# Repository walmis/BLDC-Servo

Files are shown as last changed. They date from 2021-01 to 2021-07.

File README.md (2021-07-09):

# BLDC-Servo

This project implements a FOC motor controller board for 57BLF0x series NEMA brushless motor.

The project goals are:
* to be inexpensive
* fully support FOC drive
* smooth operation for FFB devices
* Large stalled torque == relatively large current drive

The main components are:
* STM32L412 or STM32F103C8T6 MCU
* NCP81151 - MOSFET Gate drivers
* NCS213/INA213 current sense amplifiers
* FDMS8018 N-channel MOSFETS (can be any TDSON-8 30V>= MOSFETS with required current rating)
* MP2359 DC-DC step-down
* SN75176B RS485 transceiver

The board attaches directly to the motor casing with mosfets in direct contact (with thermal paste). This makes a good heatsink for power dissipation.

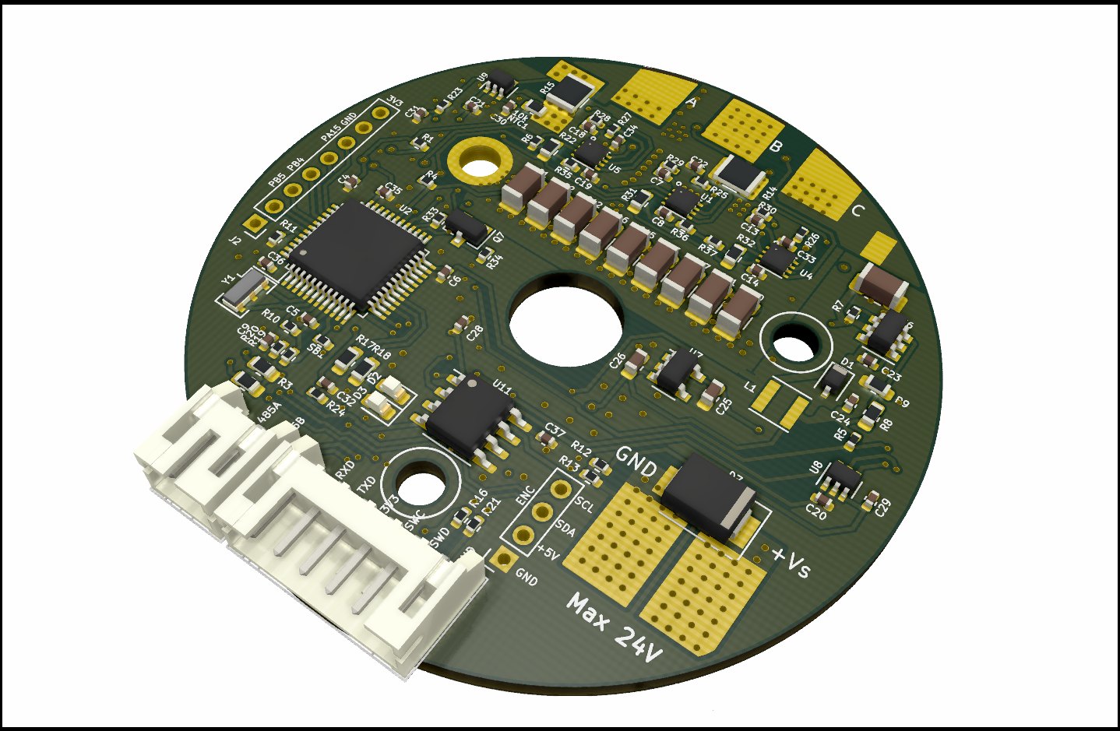
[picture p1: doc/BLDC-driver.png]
Board top

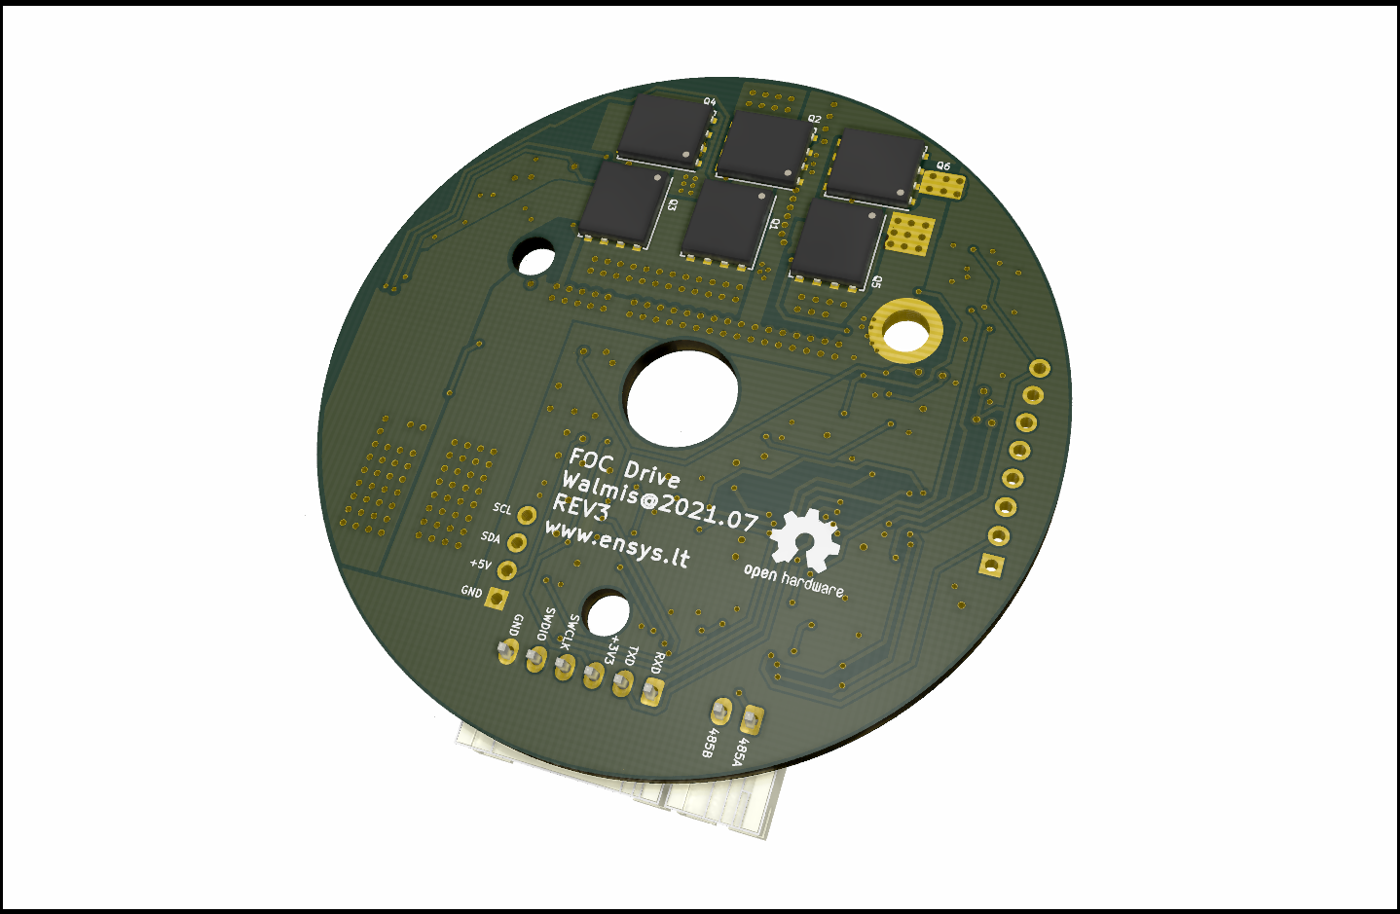
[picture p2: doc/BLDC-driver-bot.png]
Board bottom


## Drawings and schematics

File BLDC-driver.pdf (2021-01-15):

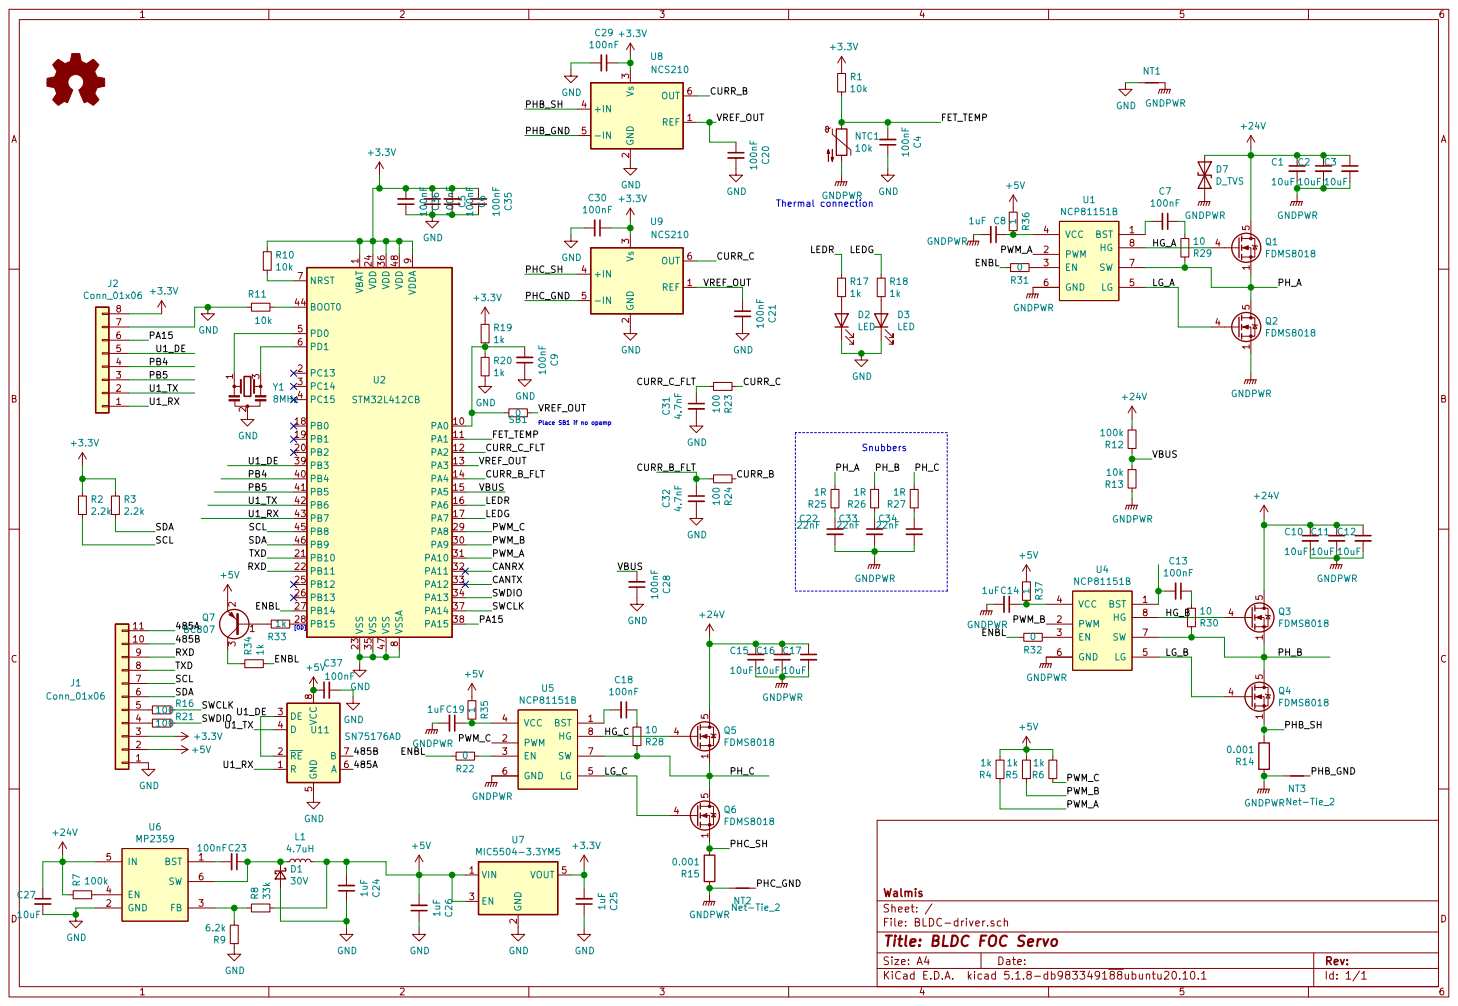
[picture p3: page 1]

1 VDD 24 VDD 36 VDD 48 VDDA

9 VSS 23 VSS 35 VSS 47 VSSA

File: BLDC-driver.sch Sheet: / Walmis

Id: 1/1 Title: BLDC FOC Servo

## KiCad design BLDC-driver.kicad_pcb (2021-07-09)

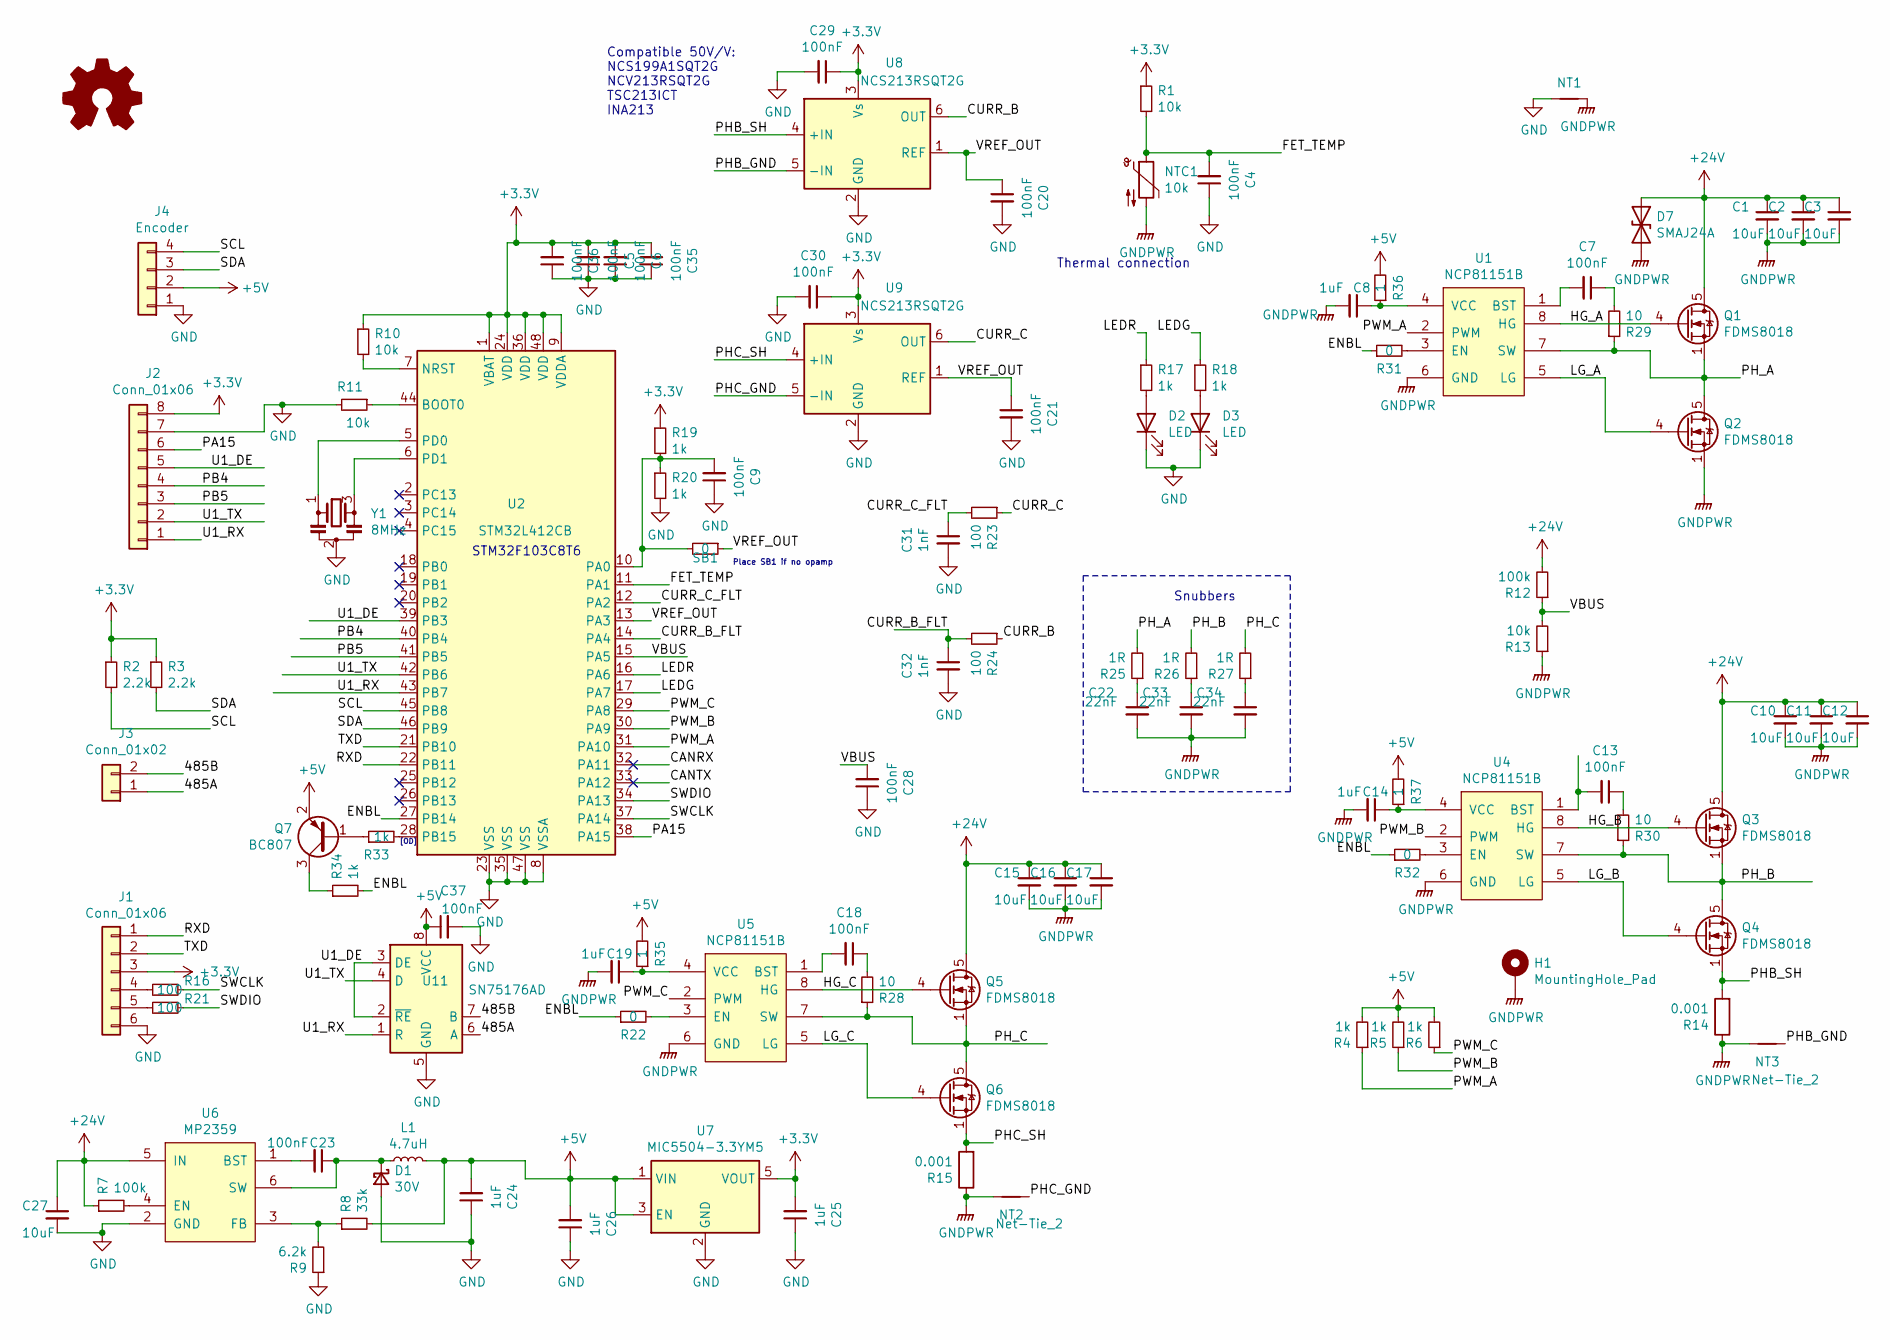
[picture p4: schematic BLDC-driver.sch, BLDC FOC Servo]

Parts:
C1, C2, C3, C10, C11, C12, C15, C16, C17, C27: 10uF; C_1206_3216Metric; JLCSMT C13585
C4, C5, C6, C7, C9, C13, C18, C20, C21, C23, C28, C29, C30, C35, C36, C37: 100nF; C_0402_1005Metric; JLCSMT C1525
C8, C14, C19, C24: 1uF; C_0402_1005Metric; JLCSMT C52923
C22, C33, C34: 22nF; C_0402_1005Metric; JLCSMT C1532
C25, C26: 1uF; C_0603_1608Metric; JLCSMT C15849
C31, C32: 1nF; C_0402_1005Metric; JLCSMT C1523
D1: 30V; D_SOD-323
D2: LED; LED_0603_1608Metric; JLCSMT C2286
D3: LED; LED_0603_1608Metric; JLCSMT C72043
D7: SMAJ24A; D_SMB; MPN SMAJ24A-E3/61
H1: MountingHole_Pad; MountingHole_3.2mm_M3_DIN965_Pad
J1: Conn_01x06; JST_PH_S6B-PH-K_1x06_P2.00mm_Horizontal
J2: Conn_01x06; PinHeader_1x08_P2.00mm_Vertical
J3: Conn_01x02; JST_PH_S2B-PH-K_1x02_P2.00mm_Horizontal
J4: Encoder; PinSocket_1x04_P2.00mm_Vertical
L1: 4.7uH; L_Taiyo-Yuden_MD-3030
NT1, NT2, NT3: Net-Tie_2; NetTie-2_SMD_Pad0.5mm
NTC1: 10k; R_0603_1608Metric; MPN NCU18XH103F60RB
Q1, Q2, Q3, Q4, Q5, Q6: FDMS8018; TDSON-8-1
Q7: BC807; SOT-23; JLCSMT C8326
R1, R10, R11, R13: 10k; R_0402_1005Metric; JLCSMT C25744
R2, R3: 2.2k; R_0603_1608Metric; JLCSMT_PKG 0603
R4, R5, R6, R19, R20, R33, R34: 1k; R_0402_1005Metric; JLCSMT_PKG 0402
R7, R12: 100k; R_0402_1005Metric; JLCSMT C25741
R8: 33k; R_0603_1608Metric; JLCSMT C4216
R9: 6.2k; R_0603_1608Metric; JLCSMT_PKG 0603
R14, R15: 0.001; R_1210_3225Metric; MPN PMR25HZPFV1L00; JLCSMT C154629
R16, R21, R23, R24: 100; R_0402_1005Metric; JLCSMT_PKG 0402
R17, R18: 1k; R_0603_1608Metric; JLCSMT_PKG 0603
R22, R31, R32: 0; R_0603_1608Metric; JLCSMT C21189
R25, R26, R27: 1R; R_0402_1005Metric; JLCSMT_PKG 0402
R28, R29, R30: 10; R_0402_1005Metric; JLCSMT_PKG 0402
R35, R36, R37: 1; R_0402_1005Metric; JLCSMT C25086
SB1: 0; R_0402_1005Metric; JLCSMT C17168
U1, U4, U5: NCP81151B; DFN-8-1EP_2x2mm_P0.5mm_EP0.9x1.5mm; MPN NCP81151MNTBG
U2: STM32L412CB; LQFP-48_7x7mm_P0.5mm
U6: MP2359; SOT-23-6; JLCSMT C14259
U7: MIC5504-3.3YM5; SOT-23-5
U8, U9: NCS213RSQT2G; SOT-363_SC-70-6
U11: SN75176AD; SOIC-8_3.9x4.9mm_P1.27mm; JLCSMT C7063
Y1: 8MHz; Resonator_SMD_muRata_CSTxExxV-3Pin_3.0x1.1mm

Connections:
+3V3: C5.2, C6.2, C25.2, C29.1, C30.1, C35.2, C36.2, J1.3, J2.8, R1.1, R2.1, R3.1, R10.1, R19.1, U2.1 (VBAT), U2.9 (VDDA), U2.24 (VDD), U2.36 (VDD), U2.48 (VDD), U7.5 (VOUT), U8.3 (Vs), U9.3 (Vs)
+5V: C24.2, C26.2, C37.1, J4.2, L1.2, Q7.2 (E), R4.2, R5.2, R6.2, R8.2, R35.2, R36.2, R37.2, U7.1 (VIN), U7.3 (EN), U11.8 (VCC)
+24V: C1.1, C2.1, C3.1, C10.1, C11.1, C12.1, C15.1, C16.1, C17.1, C27.1, D7.1 (A1), Q1.5 (D), Q3.5 (D), Q5.5 (D), R7.1, R12.2, U6.5 (IN)
/485A: J3.1, U11.6 (A)
/485B: J3.2, U11.7 (B)
/CANRX: U2.32 (PA11)
/CANTX: U2.33 (PA12)
/CURR_B: R24.1, U8.6 (OUT)
/CURR_B_FLT: C32.1, R24.2, U2.14 (PA4)
/CURR_C: R23.1, U9.6 (OUT)
/CURR_C_FLT: C31.1, R23.2, U2.12 (PA2)
/ENBL: R22.1, R31.1, R32.1, R34.2, U2.27 (PB14)
/FET_TEMP: C4.2, NTC1.1, R1.2, U2.11 (PA1)
/HG_A: Q1.4 (G), U1.8 (HG)
/HG_B: Q3.4 (G), U4.8 (HG)
/HG_C: Q5.4 (G), U5.8 (HG)
/LEDG: R18.1, U2.17 (PA7)
/LEDR: R17.1, U2.16 (PA6)
/LG_A: Q2.4 (G), U1.5 (LG)
/LG_B: Q4.4 (G), U4.5 (LG)
/LG_C: Q6.4 (G), U5.5 (LG)
/PA15: J2.6, U2.38 (PA15)
/PB4: J2.4, U2.40 (PB4)
/PB5: J2.3, U2.41 (PB5)
/PHB_GND: NT3.2, U8.5 (-IN)
/PHB_SH: Q4.1 (S), Q4.2 (S), Q4.3 (S), R14.2, U8.4 (+IN)
/PHC_GND: NT2.2, U9.5 (-IN)
/PHC_SH: Q6.1 (S), Q6.2 (S), Q6.3 (S), R15.2, U9.4 (+IN)
/PH_A: Q1.1 (S), Q1.2 (S), Q1.3 (S), Q2.5 (D), R25.2, R29.1, U1.7 (SW)
/PH_B: Q3.1 (S), Q3.2 (S), Q3.3 (S), Q4.5 (D), R26.2, R30.1, U4.7 (SW)
/PH_C: Q5.1 (S), Q5.2 (S), Q5.3 (S), Q6.5 (D), R27.2, R28.1, U5.7 (SW)
/PWM_A: R4.1, U1.2 (PWM), U2.31 (PA10)
/PWM_B: R5.1, U2.30 (PA9), U4.2 (PWM)
/PWM_C: R6.1, U2.29 (PA8), U5.2 (PWM)
/RXD: J1.1, U2.22 (PB11)
/SCL: J4.4, R2.2, U2.45 (PB8)
/SDA: J4.3, R3.2, U2.46 (PB9)
/SWCLK: R16.1, U2.37 (PA14)
/SWDIO: R21.1, U2.34 (PA13)
/TXD: J1.2, U2.21 (PB10)
/U1_DE: J2.5, U2.39 (PB3), U11.2 (~RE), U11.3 (DE)
/U1_RX: J2.1, U2.43 (PB7), U11.1 (R)
/U1_TX: J2.2, U2.42 (PB6), U11.4 (D)
/VBUS: C28.2, R12.1, R13.2, U2.15 (PA5)
/VREF_OUT: C20.1, C21.1, SB1.1, U2.13 (PA3), U8.1 (REF), U9.1 (REF)
GND: C4.1, C5.1, C6.1, C9.1, C20.2, C21.2, C24.1, C25.1, C26.1, C27.2, C28.1, C29.2, C30.2, C31.2, C32.2, C35.1, C36.1, C37.2, D1.2 (A), D2.1 (K), D3.1 (K), J1.6, J2.7, J4.1, NT1.1, R9.1, R11.2, R20.2, U2.8 (VSSA), U2.23 (VSS), U2.35 (VSS), U2.47 (VSS), U6.2 (GND), U7.2 (GND), U8.2 (GND), U9.2 (GND), U11.5 (GND), Y1.2
GNDPWR: C1.2, C2.2, C3.2, C8.2, C10.2, C11.2, C12.2, C14.2, C15.2, C16.2, C17.2, C19.2, C22.2, C33.2, C34.2, D7.2 (A2), H1.1, NT1.2, NT2.1, NT3.1, NTC1.2, Q2.1 (S), Q2.2 (S), Q2.3 (S), R13.1, R14.1, R15.1, U1.6 (GND), U1.9 (PAD), U4.6 (GND), U4.9 (PAD), U5.6 (GND), U5.9 (PAD)
unnamed: C7.1, R29.2
unnamed: C7.2, U1.1 (BST)
unnamed: C8.1, R36.1, U1.4 (VCC)
unnamed: C9.2, R19.2, R20.1, SB1.2, U2.10 (PA0)
unnamed: C13.1, R30.2
unnamed: C13.2, U4.1 (BST)
unnamed: C14.1, R37.1, U4.4 (VCC)
unnamed: C18.1, R28.2
unnamed: C18.2, U5.1 (BST)
unnamed: C19.1, R35.1, U5.4 (VCC)
unnamed: C22.1, R25.1
unnamed: C23.1, D1.1 (K), L1.1, U6.6 (SW)
unnamed: C23.2, U6.1 (BST)
unnamed: C33.1, R26.1
unnamed: C34.1, R27.1
unnamed: D2.2 (A), R17.2
unnamed: D3.2 (A), R18.2
unnamed: J1.4, R16.2
unnamed: J1.5, R21.2
unnamed: Q7.1 (B), R33.1
unnamed: Q7.3 (C), R34.1
unnamed: R7.2, U6.4 (EN)
unnamed: R8.1, R9.2, U6.3 (FB)
unnamed: R10.2, U2.7 (NRST)
unnamed: R11.1, U2.44 (BOOT0)
unnamed: R22.2, U5.3 (EN)
unnamed: R31.2, U1.3 (EN)
unnamed: R32.2, U4.3 (EN)
unnamed: R33.2, U2.28 (PB15)
unnamed: U2.5 (PD0), Y1.1
unnamed: U2.6 (PD1), Y1.3

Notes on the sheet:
Thermal connection
Snubbers
Place SB1 if no opamp
[OD]
Compatible 50V/V: NCS199A1SQT2G NCV213RSQT2G TSC213ICT INA213
STM32F103C8T6

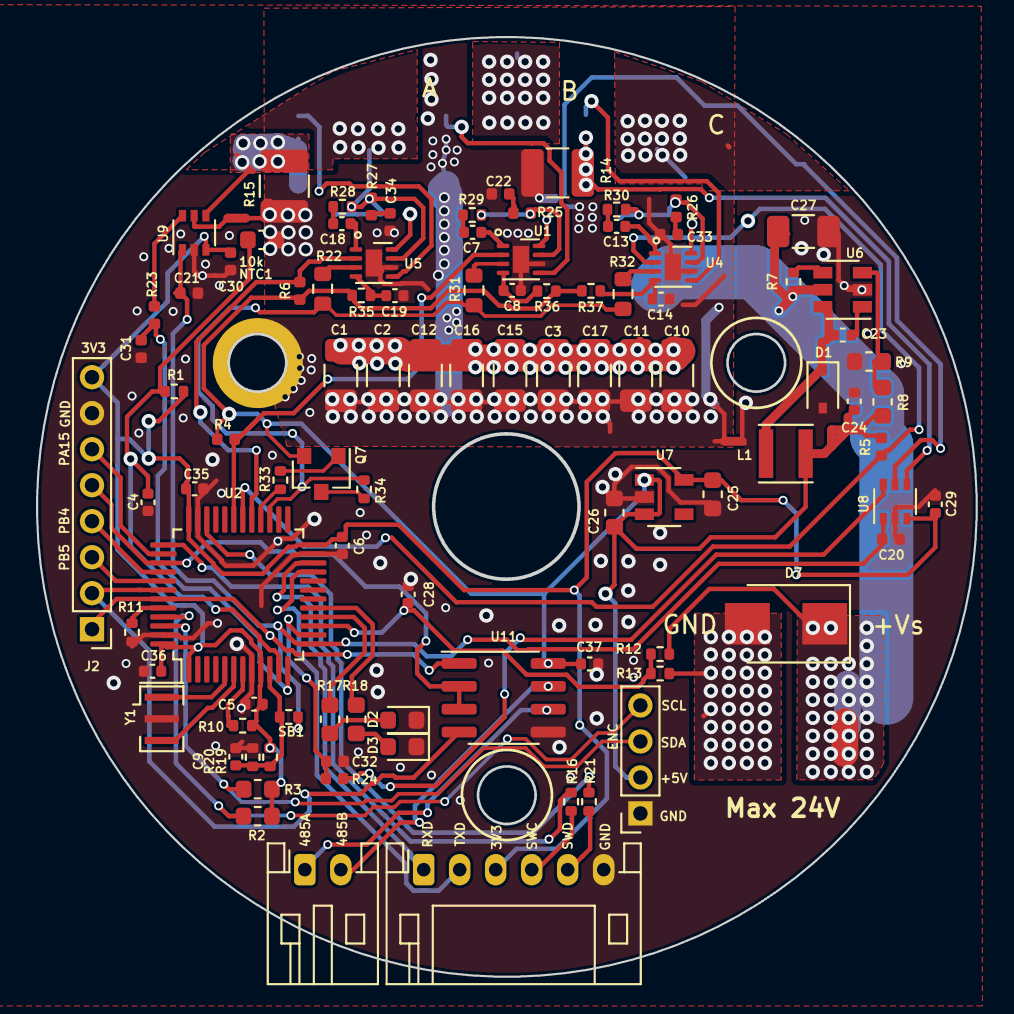
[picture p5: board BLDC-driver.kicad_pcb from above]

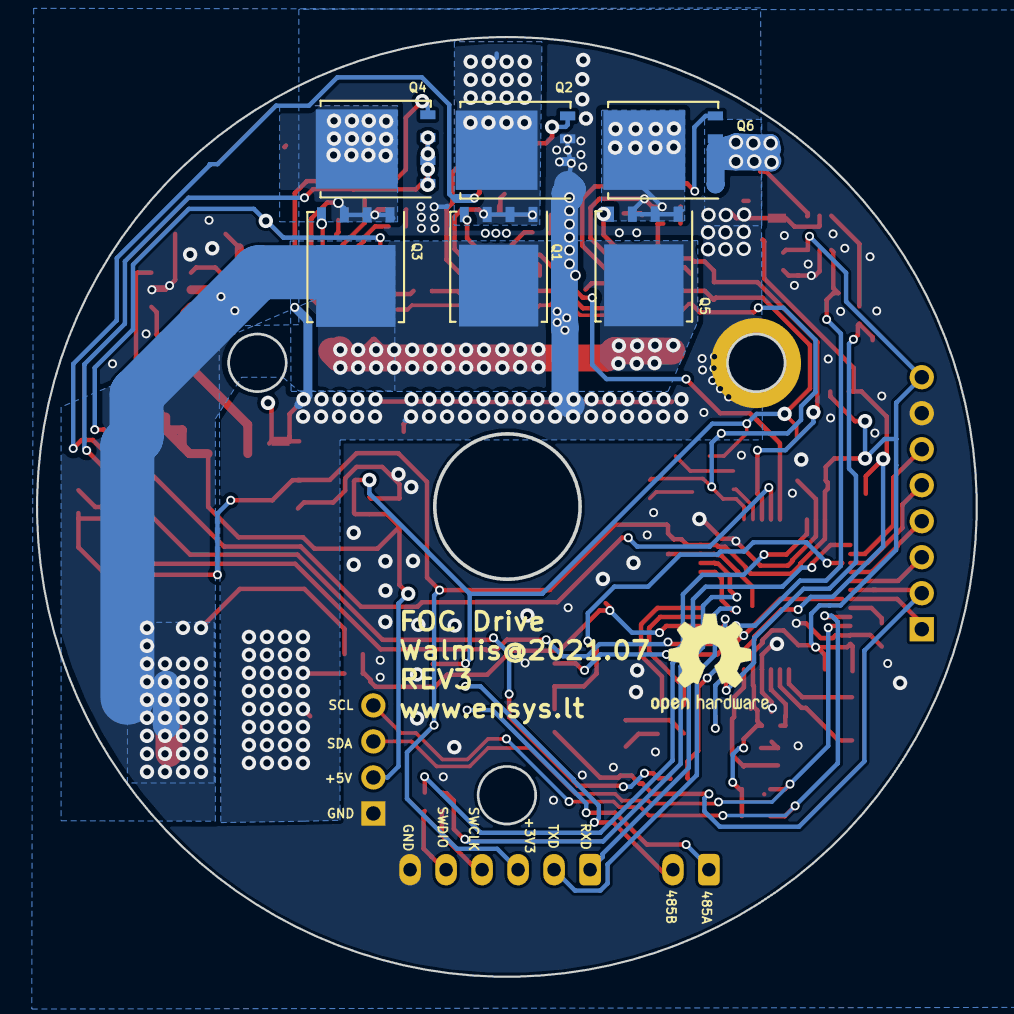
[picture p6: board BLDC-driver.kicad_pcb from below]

Board: 2 copper layers, 52.2 x 52.2 mm, 106 parts (7 on the bottom side), 76 nets.

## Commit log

2020-06-15 Schematic progress
    [BLDC-driver.kicad_pcb, BLDC-driver.sch]
2020-06-18 Change to stm32f103c8t6
    [BLDC-driver.kicad_pcb, BLDC-driver.sch]
2020-06-29 Change i2c resistor to 2.2k
    [BLDC-driver.kicad_pcb, BLDC-driver.sch]
2020-07-05 add pwm 5v pull up
    [BLDC-driver.kicad_pcb, BLDC-driver.sch]
2020-07-07 Add snubbers
    [BLDC-driver.kicad_pcb, BLDC-driver.sch]
2021-01-15 Revision 2 update
    Move current shunts to low side. I have encountered smoke from current
    amplifiers when working @ 20V.
    Adapt to STM32L4xxCBT mcu.
    Add snubbers and resistance to gate drivers to reduce ringing due to
    very fast switching.
    Add RS485 interface instead of CAN
    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
    [BLDC-driver.kicad_pcb, BLDC-driver.sch]
2021-01-15 Add schematic pdf
2021-01-15 Add MPNs for some parts
    [BLDC-driver.sch]
2021-07-09 Multiple updates:
    Change amp filter caps to 1nF
    Move second shunt resistor to top layer
    Make one hole grounded
    various routing updates
    [BLDC-driver.kicad_pcb, BLDC-driver.sch]
2021-07-09 Rev3: Update connectors, add JST PH connectors
    [BLDC-driver.kicad_pcb, BLDC-driver.sch]
2021-07-09 Update images, readme
    [BLDC-driver.kicad_pcb]
